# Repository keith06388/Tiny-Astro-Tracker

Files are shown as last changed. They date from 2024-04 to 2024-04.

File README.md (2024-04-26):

# Tiny-Astro-Tracker
Equatorial tracker for cell phone astrophotography
### Features

- Star tracking for backpacking astrophotography, rotation at sidereal tracking rate
- Integrated green laser diode for polar alignment
- Selector switch for hemisphere direction
- USB-C powered to minimize tracker weight
- TMC 2300 driven bipolar stepper motor with microstepping for smooth and silent operation
- 31,930:1 total gear ratio from stepper motor to output to minimize motor size
  - 1030:1 gearbox sourced with motor
  - 31:1 custom designed harmonic gearbox integrated into design
- Custom PCB for motor drive, laser drive, laser on/off switch input, hemisphere selection switch
- XIAO nRF52840 control board for low power consumption, accurate clock for speed control, and bluetooth for future expansion



### Parts List

Purchased:
- Motor with gearbox - https://www.aliexpress.us/item/3256805825353915.html
- Thin section bearing - 6706 2RS - https://www.aliexpress.us/item/3256801627556831.html
- Laser diode - https://www.aliexpress.us/item/3256804645031555.html
- Laser control switch (9mm) - https://www.aliexpress.us/item/2251832725948381.html
- Threaded inserts - McMaster 94674A537 - https://www.mcmaster.com/catalog/130/3662/94674A537
- Delrin 5mm bearing balls - https://www.aliexpress.us/item/3256803525375798.html

3D Printed Parts in ASA:
- Housing (paused printing to install thread insert)
- Output (paused printing to install thread insert)
- Flex spline
- Wave generator

PCB:
- Seeed Studio XIAO nRF52840 - https://www.seeedstudio.com/Seeed-XIAO-BLE-nRF52840-p-5201.html
- Custom breakout/motor and laser drive sourced through JLCPCB

Recommended accessories:
- Novoflex micropod - https://www.bhphotovideo.com/c/product/269751-REG/Novoflex_MICROPOD.html
- PGYTECH Mini Smartphone Holder - https://www.bhphotovideo.com/c/product/1645233-REG/pgytech_p_cg_012_mini_phone_holder.html
- koolehaoda 1/4 Mini BallHead (for mounting astro tracker) - https://www.amazon.com/koolehaoda-BallHead-Adapter-Camera-Monopod/dp/B01L94BK3Q
- SIOTI Mini Ball Head (for phone mount, better adjustability than koolehaoda) - https://www.amazon.com/SIOTI-Adapter-Compatiable-Digital-Microphone/dp/B0B313GM4H
- Carbon fiber tube to swap for legs in Novoflex micropod (6x4mm, swapped for weight savings) - https://www.aliexpress.us/item/3256804190926981.html











20230202_163712(1)

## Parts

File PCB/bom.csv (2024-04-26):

Designator | Footprint | Quantity | Value | LCSC Part #
C1 | C_0805_2012Metric | 1 | 10µF/25V/0805
C2 | C_0603_1608Metric | 1 | 100nF/25V/0603 | C14663
C3, C4 | C_0603_1608Metric | 2 | 100nF/5V/0603 | C14663
C5, C6 | C_0603_1608Metric | 2 | 1uF/10V/0603 | C15849
C7 | C_0805_2012Metric | 1 | 47µF/25V/0805 | C16780
D1 | D_SOD-323 | 1 | Schottky | C191023
IC1 | TMC2300 | 1 | TMC2300 | C516356
L1 | LQH44PN470MJ0L | 1 | 47uH | C341779
R1, R2 | R_0603_1608Metric | 2 | 1Ω/0,1W/0603 | C22936
R3 | R_0402_1005Metric | 1 | 1kΩ/1%/0402 | C11702
R4 | R_0402_1005Metric | 1 | 100kΩ/1%/0402 | C25741
R5 | R_0402_1005Metric | 1 | 150kΩ/1%/0402 | C25755
R6 | R_0603_1608Metric | 1 | 1Ω/1%/0603 | C22936
SW2 | SSSS811101 | 1 | SW_SPDT | C109335
U2 | LM3407MY | 1 | LM3407MY | C543051

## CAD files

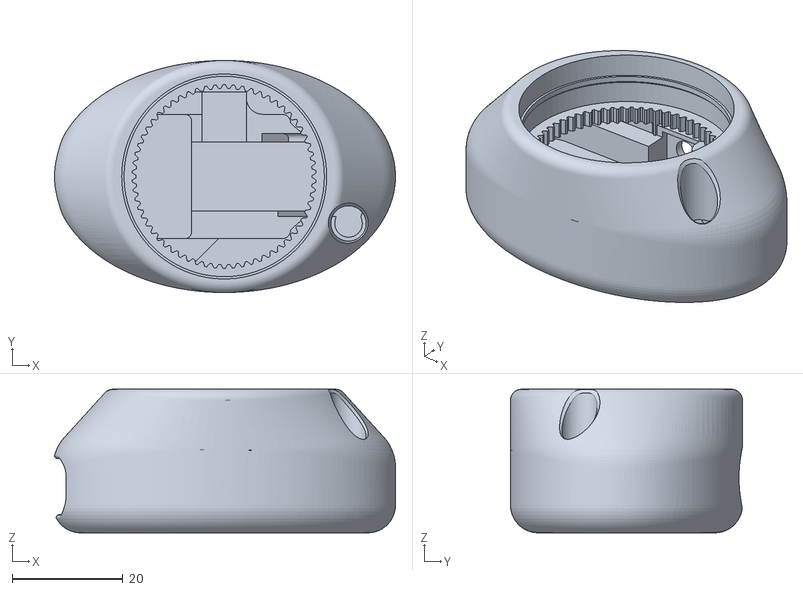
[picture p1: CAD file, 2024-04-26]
STLS/Housing.stl
61.7 x 42.0 x 26.0

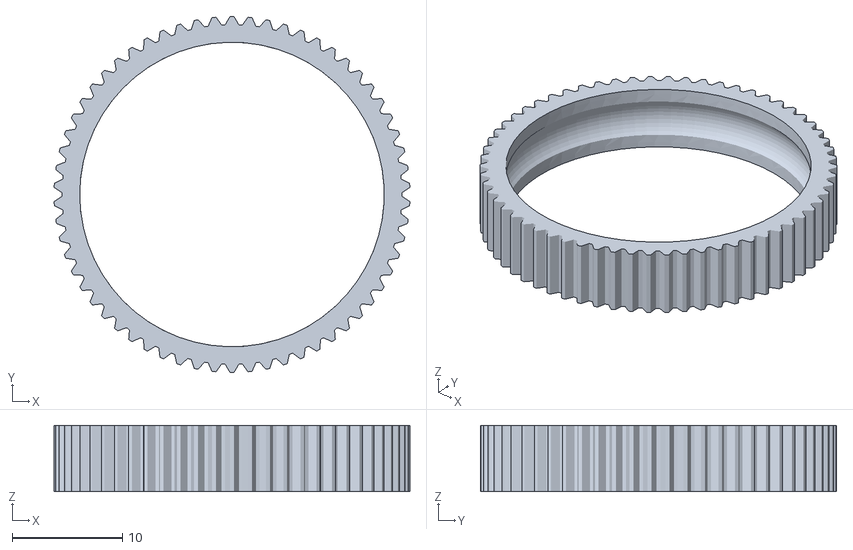
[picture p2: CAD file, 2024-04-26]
STLS/Flex_Spline.stl
32.3 x 32.3 x 6.00

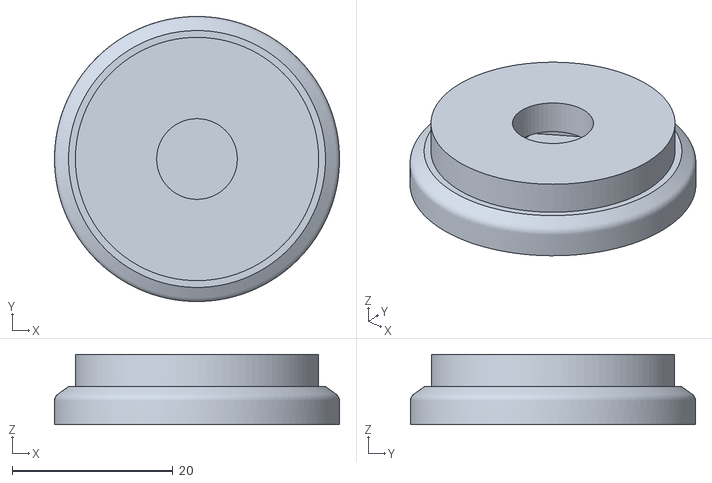
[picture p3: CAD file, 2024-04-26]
STLS/Output.stl
35.5 x 35.5 x 8.75

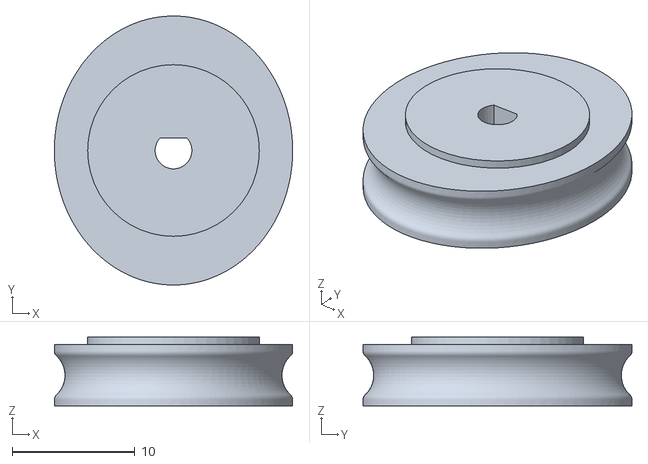
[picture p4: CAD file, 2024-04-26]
STLS/Wave_Generator.stl
19.4 x 21.9 x 5.62

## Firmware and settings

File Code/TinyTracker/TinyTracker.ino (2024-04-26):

#include "include/Functions.h"
#include "include/TMC2300.h"
#include "include/CRC.h"
#include "Adafruit_TinyUSB.h"
#include "nRF52_PWM.h"

// Important these are the I/O pin values not the physical pin values
#define LED_STATUS LED_BUILTIN 
#define MOTOR_EN 8 
#define MOTOR_STEP 9
#define MOTOR_DIR 10
#define SW1 0
#define SW2 1
#define LSR 2
#define DIM 3
#define _PWM_LOGLEVEL_       1
#define USING_TIMER       false   //true
#define pinToUse       MOTOR_STEP

//creates pwm instance
nRF52_PWM* PWM_Instance;
float frequency = 23720.0f;
float dutyCycle = 50.0f;
int ledState = LOW;        // the current state of the output pin
int buttonState;            // the current reading from the input pin
int lastButtonState = LOW;  // the previous reading from the input pin
int speed = LOW;            // the motor speed
unsigned long lastDebounceTime = 0;  // the last time the output pin was toggled
unsigned long debounceDelay = 50;    // the debounce time; increase if the output flickers
unsigned long pressDelay = 1500;    // the long press delay time
unsigned long timeout = 15000;    // auto turn off time
unsigned long ontime = 0;    // last time the light was turned on


void tmc2300_current(int currentInt)   
{    
  uint32_t value = 1 << TMC2300_IHOLDDELAY_SHIFT    
                 | ((currentInt << TMC2300_IRUN_SHIFT) & TMC2300_IRUN_MASK)    
                 | 8 << TMC2300_IHOLD_SHIFT;    
  tmc2300_writeInt(TMC2300_IHOLD_IRUN, value);  
}    

void setup() {
  Serial.begin(9600);

  pinMode(LED_STATUS, OUTPUT);
  pinMode(MOTOR_EN, OUTPUT);
  pinMode(MOTOR_STEP,OUTPUT);    
  pinMode(MOTOR_DIR,OUTPUT);  
  pinMode(SW2,INPUT_PULLUP);  

// Disable the motor
  digitalWrite(MOTOR_EN, LOW);   
  digitalWrite(MOTOR_STEP,LOW);  
  digitalWrite(MOTOR_DIR,digitalRead(SW2));    

// TMC2300 IC UART connection
  Serial1.begin(115200);
  delay(1000);

// Initialize CRC calculation for TMC2300 UART datagrams
  tmc_fillCRC8Table(0x07, true, 0);
  tmc2300_writeInt(TMC2300_CHOPCONF, 0x13008001);  // Re-write the CHOPCONF back to the default
  tmc2300_writeInt(TMC2300_PWMCONF, 0xC40F1024);
  tmc2300_current(31);
  digitalWrite(MOTOR_EN, HIGH);   


//assigns PWM frequency of 1.0 KHz and a duty cycle of 0%
  PWM_Instance = new nRF52_PWM(pinToUse, frequency, dutyCycle);
  
  pinMode(SW1, INPUT_PULLUP);
  pinMode(LSR, OUTPUT);
  pinMode(DIM, OUTPUT);
  digitalWrite(LSR, ledState);
  digitalWrite(DIM, HIGH);  

}

void loop() {
  // read the state of the switch into a local variable:
  int reading = !digitalRead(SW1);

  // check to see if you just pressed the button
  // (i.e. the input went from LOW to HIGH), and you've waited long enough
  // since the last press to ignore any noise:

  // If the switch changed, due to noise or pressing:
  if (reading != lastButtonState) {
    // reset the debouncing timer
    lastDebounceTime = millis();      
    }


  if ((millis() - lastDebounceTime) > debounceDelay) {
    // whatever the reading is at, it's been there for longer than the debounce
    // delay, so take it as the actual current state:

    // if the button state has changed:
    if (reading != buttonState) {
      buttonState = reading;

      // only toggle the LED if the new button state is HIGH
      if (buttonState == HIGH) {
        ledState = !ledState;
        ontime = millis();
      }
    }

  }

  // set the LED:
  if ((millis()-ontime) > timeout){
    ledState = false;
  }
  
  digitalWrite(LSR, ledState);

  // save the reading. Next time through the loop, it'll be the lastButtonState:
  lastButtonState = reading;
}

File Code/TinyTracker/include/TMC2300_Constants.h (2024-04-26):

/*
 * TMC2300_Constants.h
 *
 *  Created on: 16.01.2019
 *      Author: LK
 */

#ifndef TMC_IC_TMC2300_TMC2300_CONSTANTS_H_
#define TMC_IC_TMC2300_TMC2300_CONSTANTS_H_

#define TMC2300_MOTORS           1
#define TMC2300_REGISTER_COUNT   TMC_REGISTER_COUNT
#define TMC2300_WRITE_BIT        TMC_WRITE_BIT
#define TMC2300_ADDRESS_MASK     TMC_ADDRESS_MASK
#define TMC2300_MAX_VELOCITY     s32_MAX
#define TMC2300_MAX_ACCELERATION u24_MAX

#endif /* TMC_IC_TMC2300_TMC2300_CONSTANTS_H_ */
